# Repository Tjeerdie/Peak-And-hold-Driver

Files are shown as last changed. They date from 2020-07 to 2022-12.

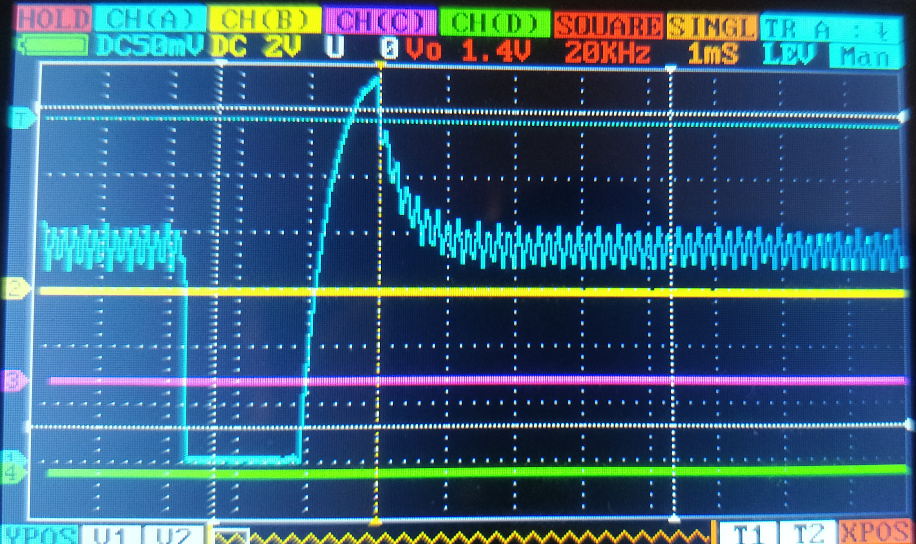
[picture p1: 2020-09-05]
Measurements/CoilCurrent_85procentDutycycle4500RPM3.5APeak2.0AHold.jpg

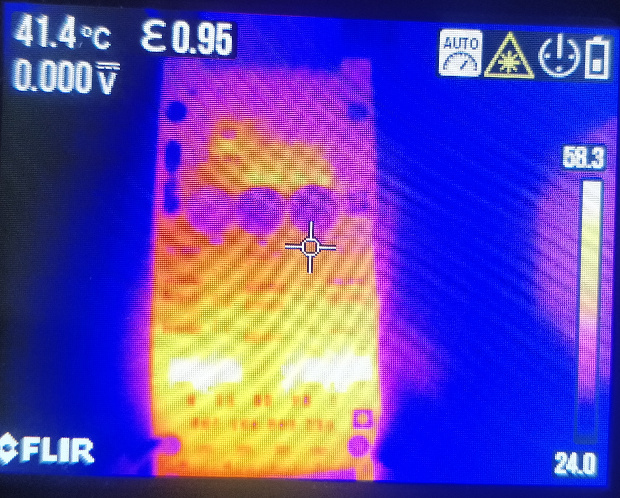
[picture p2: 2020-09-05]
Measurements/HeatMap_85procentDutycycle4500RPM3.5APeak1.0AHold.jpg

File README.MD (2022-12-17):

# Project PWM peak and hold injector driver
The peak and hold project started because I could not find an open-source PWM peak and hold injector driver for low-Z injectors. For low-z injectors normally resistors in series with the injectors are used. But resistors create a lot of heat and are not very adjustable. 

I still do encourage everyone to use resistors if possible because the results are good and resistors have less components that can fail<br/>
<br/>
This design is specific to work with LPG injectors but could be used for any other low-Z injectors like TBI type and other high flow injectors. It could even be used for any coil type actuator like relays or valves <br/>

The board is designed in Kicad. So to see the schematic or to adjust the design to your liking open the Kicad project.<br/>

Latest release is V0.3.1<br/>
__IMPORANT NOTE: Board V0.3.1 is not tested yet!! A modified V0.3 is used for bench testing the V0.3.1 schematic. I did not test the board on a car yet__<br/>
__specifications:__
- Max peak current ~5A<br/>
- Max continuous hold current ~1A (No extra cooling)<br/>
- Max continuous hold current ~2A (With extra cooling)<br/>
- Hold PWM duty cycle 5%-95%<br/>
- PWM frequency 7khz<br/>
- 4 Individual injector channels<br/>
- Peak and hold current are adjustable

## Getting Started
This section explains all we need to do to setup a fabricated PCB

### Get all the parts
1. Order the PCB. For example use https://www.pcbway.com/ or https://jlcpcb.com/ Upload the PeakHoldPWMDriver_V0.x.y.zip located in the gebers folder and order the design.<br/>
2. Get all the parts from you favorite supplier. A BOM list is included in the geber folder<br/>
3. Assemble the PCB, hand soldering is possible.<br/>

### Connect the board
The board is intended to be connected to any ECU that uses a switch to ground for each injector channel. This is the case for most types of ECU. Further down this readme there is a description how to use microcontroller pins to drive the injectors directly. <br/>

__Connector J1__
1. injector channel 1 IN<br/>
2. injector channel 2 IN<br/>
3. injector channel 3 IN<br/>
4. injector channel 4 IN<br/>
5. Power - <br/>
6. Power + (14.8V switched with ignition switch)<br/>

__Connector J2__
1. inj channel 1 +<br/>
2. inj channel 1 -<br/>
3. inj channel 2 +<br/>
4. inj channel 2 -<br/>
5. inj channel 3 +<br/>
6. inj channel 3 -<br/>
7. inj channel 4 +<br/>
8. inj channel 4 -<br/>

Power on the board. Led must be lit when powered.<br/>

### Set the PEAK current
1. Measure __TP1__ and use __RV2__ to set to value needed. 100mV = 1A<br/>
2. Make sure this PEAK current is not too close to the maximum current. If that is the case you run the risk the peak current is never reached and the HOLD current is never set. Maximum advised peak current = 10.0[V] / R-inj[Ohm]<br/>

### Set the HOLD current
1. Measure the resistance of the injector(s) per channel (R-inj)[Ohm]. <br/>
2. Find the hold current needed for the injector in the datasheet. Usually about 50% to 25% of the peak current would be enough<br/>
3. Calculate the duty cycle needed using: ((R-inj + 0.20)* HoldCurrent)/2,4<br/>
4. Measure __TP2__ and use __RV1__ to set it to voltage calculated in step 3.<br/>
5. If it is possible in your setup or on a bench, connect __injector channel 1 IN__ to the __Power -__ use a multi-meter in series with your connected injector on channel 1 to measure the current. This must be close the the set current. If this is not correct adjust __RV1__ accordingly. Be careful when doing this test! When fuel pressure is present during testing the injector under test wil spray (a lot) of fuel! Its best to test with not pressurised injectors<br/>

### Direct microcontroller input
It is possible to use the board directly with an microcontroller. (non inverted inputs) The board inputs are designed for 5V. 3.3V can work but is on the edge so any voltage drop or temperature change may make it stop working correctly. <br/>

With a sharp object scratch the bridge between __pin 1__ and __pin 2__ of __JP1__, __JP2__, __JP3__, __JP4__ on the back of the board. Use a multi-meter to double check the connection is broken. Use a soldering iron and a bit of solder to connect __pin 3__ and __pin 2__ for __JP1__ to __JP4__. The second step is to remove R8, R25, R11, R28 from the board<br/> 
       
## Simulation	
An LTspice simulation of PWM peak and hold drivers is also in the LTspice folder. It is a good learning experience to see the wave forms and the current thru the coil. This also shows the maximum voltage level expected on the mosfets. This can be significant voltage levels depdending on the clamping voltage of the main driver. <br/>

## License
This project is licensed under the GNU GENERAL PUBLIC LICENSE - see the [LICENSE.md](LICENSE.md) file for details<br/>

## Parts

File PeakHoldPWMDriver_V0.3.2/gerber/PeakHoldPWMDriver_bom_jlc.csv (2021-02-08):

Comment | Designator | Footprint | LCSC Part #
1mF | C3,C2,C1 | CP_Elec_10x12.5 | C249474
220nf | C6,C5,C14,C12,C11,C10,C9,C13,C8 | C_0603_1608Metric_Pad1.05x0.95mm_HandSolder | C21120
10uf | C7,C4 | C_1206_3216Metric_Pad1.42x1.75mm_HandSolder | C13585
LL4148 | D3 | D_MiniMELF | C9808
BLUE | D4 | LED_0603_1608Metric_Pad1.05x0.95mm_HandSolder | C375446
BAT54S | D6,D14,D13,D5 | SOT-23 | C19726
SS36 | D20,D19,D12,D11 | D_SMC | C35722
PPTC 16V2A | F2 | Fuse_1812_4532Metric_Pad1.30x3.40mm_HandSolder | C70115
TSM2309 | Q5,Q15,Q13,Q6,Q19,Q17,Q18,Q20 | SOT-23 | C15127
2N7002 | Q12,Q11,Q4,Q1,Q2,Q10,Q9,Q3 | SOT-23 | C8545
IRLL 024N | Q16,Q14,Q8,Q7 | SOT-223 | C189606
470k | R3 | R_0603_1608Metric_Pad1.05x0.95mm_HandSolder | C23178
100k | R4 | R_0603_1608Metric_Pad1.05x0.95mm_HandSolder | C25803
15k | R5 | R_0603_1608Metric_Pad1.05x0.95mm_HandSolder | C22809
470R | R6,R32,R35,R34,R16,R19,R15,R17,R7,R9,R12,R29,R31,R26 | R_0603_1608Metric_Pad1.05x0.95mm_HandSolder | C23179
10K | R8,R11,R28,R25,R44,R43,R41 | R_0603_1608Metric_Pad1.05x0.95mm_HandSolder | C25804
10k | R10 | R_0603_1608Metric_Pad1.05x0.95mm_HandSolder | C25804
0R1 | R22,R38,R21,R37 | R_2512_6332Metric_Pad1.52x3.35mm_HandSolder | C76254
1K | R24,R39,R40,R23,R13,R14,R30,R27,R42 | R_0603_1608Metric_Pad1.05x0.95mm_HandSolder | C21190
100R | R33,R36,R20,R18 | R_0603_1608Metric_Pad1.05x0.95mm_HandSolder | C22775
120k | R45 | R_0603_1608Metric | C25808
33k | R47 | R_0603_1608Metric | C4216
74HC32 | U1 | SO-14_5.3x10.2mm_P1.27mm | C5632
LM2901 | U2 | SO-14_5.3x10.2mm_P1.27mm | C163545
LTC6992 | U4 | SOT-23-6_Handsoldering | C117381
74HC74 | U5,U3 | SO-14_5.3x10.2mm_P1.27mm | C7345
LM340 | U6 | SOT-223-3_TabPin2 | C131990
74HC08 | U7,U8 | SO-14_5.3x10.2mm_P1.27mm | C5593

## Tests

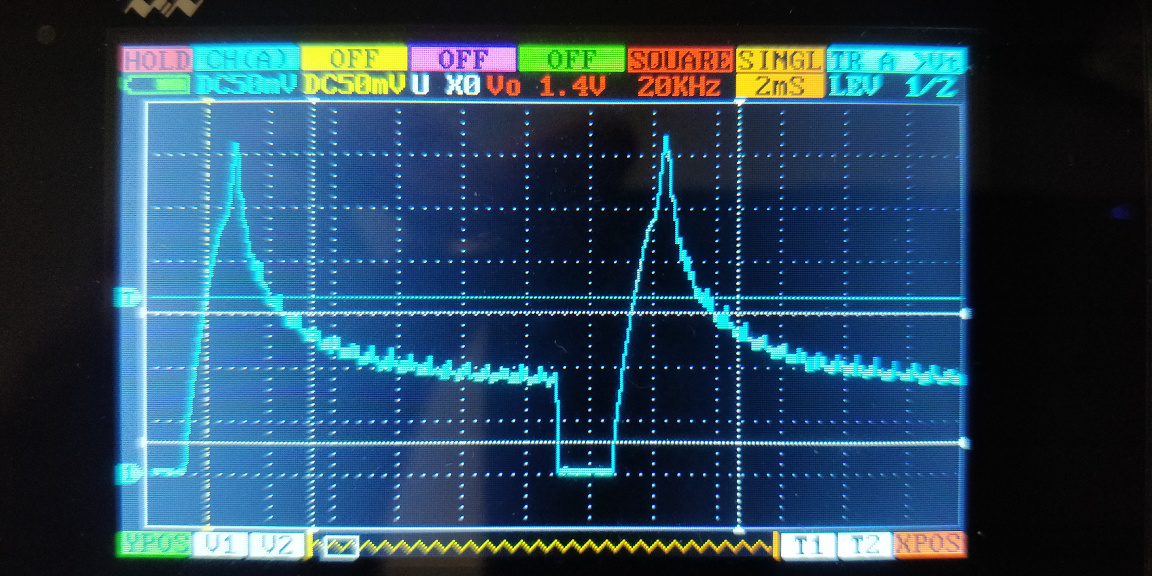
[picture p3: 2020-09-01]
Measurements/CoilCurrent_95procentDutycycle4500RPM3.5APeak0.8AHold.jpg

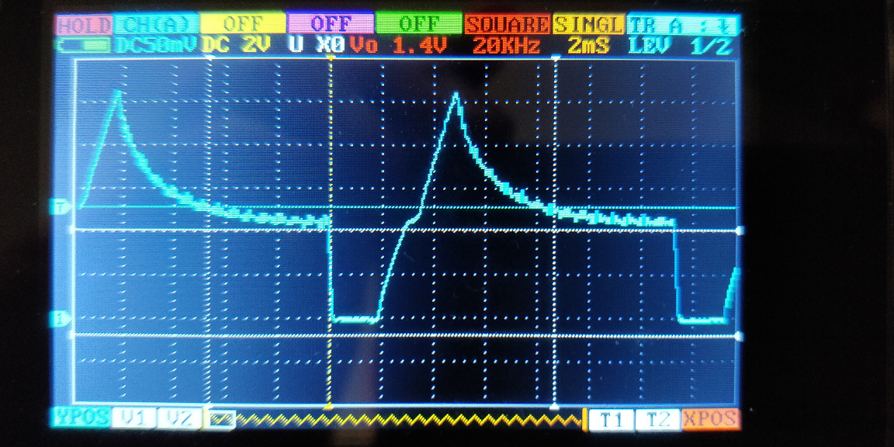
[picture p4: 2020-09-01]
Measurements/CoilCurrent_95procentDutycycle4500RPM2.5APeak1.1AHold.jpg

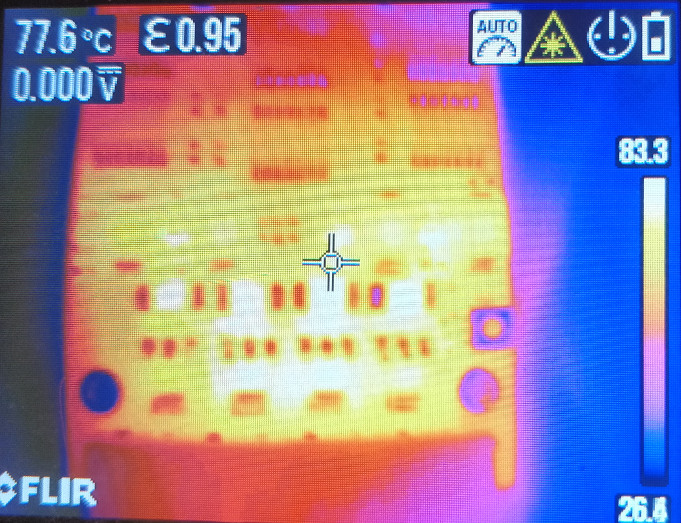
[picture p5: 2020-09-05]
Measurements/HeatMap_85procentDutycycle4500RPM3.5APeak2.0AHold.jpg

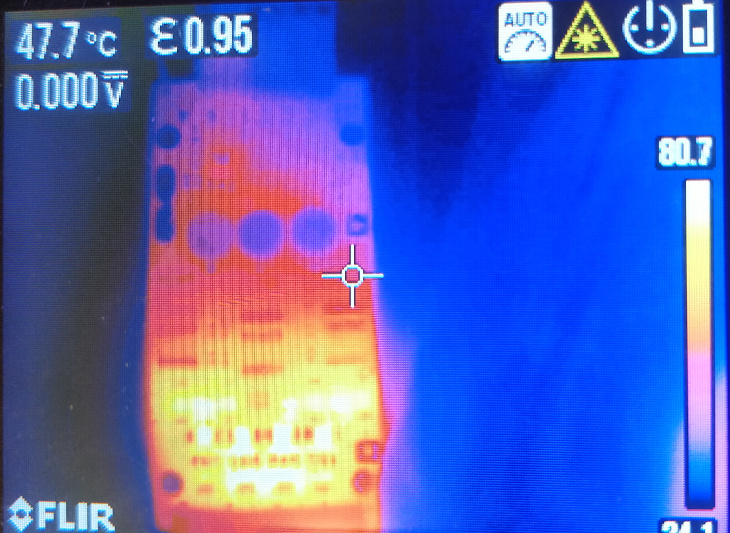
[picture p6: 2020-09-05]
Measurements/HeatMap_85procentDutycycle4500RPM3.5APeak2.0AHold_2.jpg

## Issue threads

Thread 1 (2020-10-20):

TSM2309

hugovw1976, 2020-10-20:
Hi, just curious why you use two TSM2309 in parallel.

Tjeerdie, 2020-10-20:
There is little more explanation on the speeduino forum for this board.

The reasoning is heat dissipation. Its a sot23 package. Two parallel will
give you half the Rds on and two packages to get the heat out. With 1A you
maybe get away with one.

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

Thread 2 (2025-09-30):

BOM and CPL not matching

alexsve1990, 2025-09-30:
I'm trying to upload the BOM and CPL file after I have uploaded the Gerber file. I get a mismatch with some components missing in the BOM file and sometimes I also get error messages. I also tried with different versions of Gerber file.

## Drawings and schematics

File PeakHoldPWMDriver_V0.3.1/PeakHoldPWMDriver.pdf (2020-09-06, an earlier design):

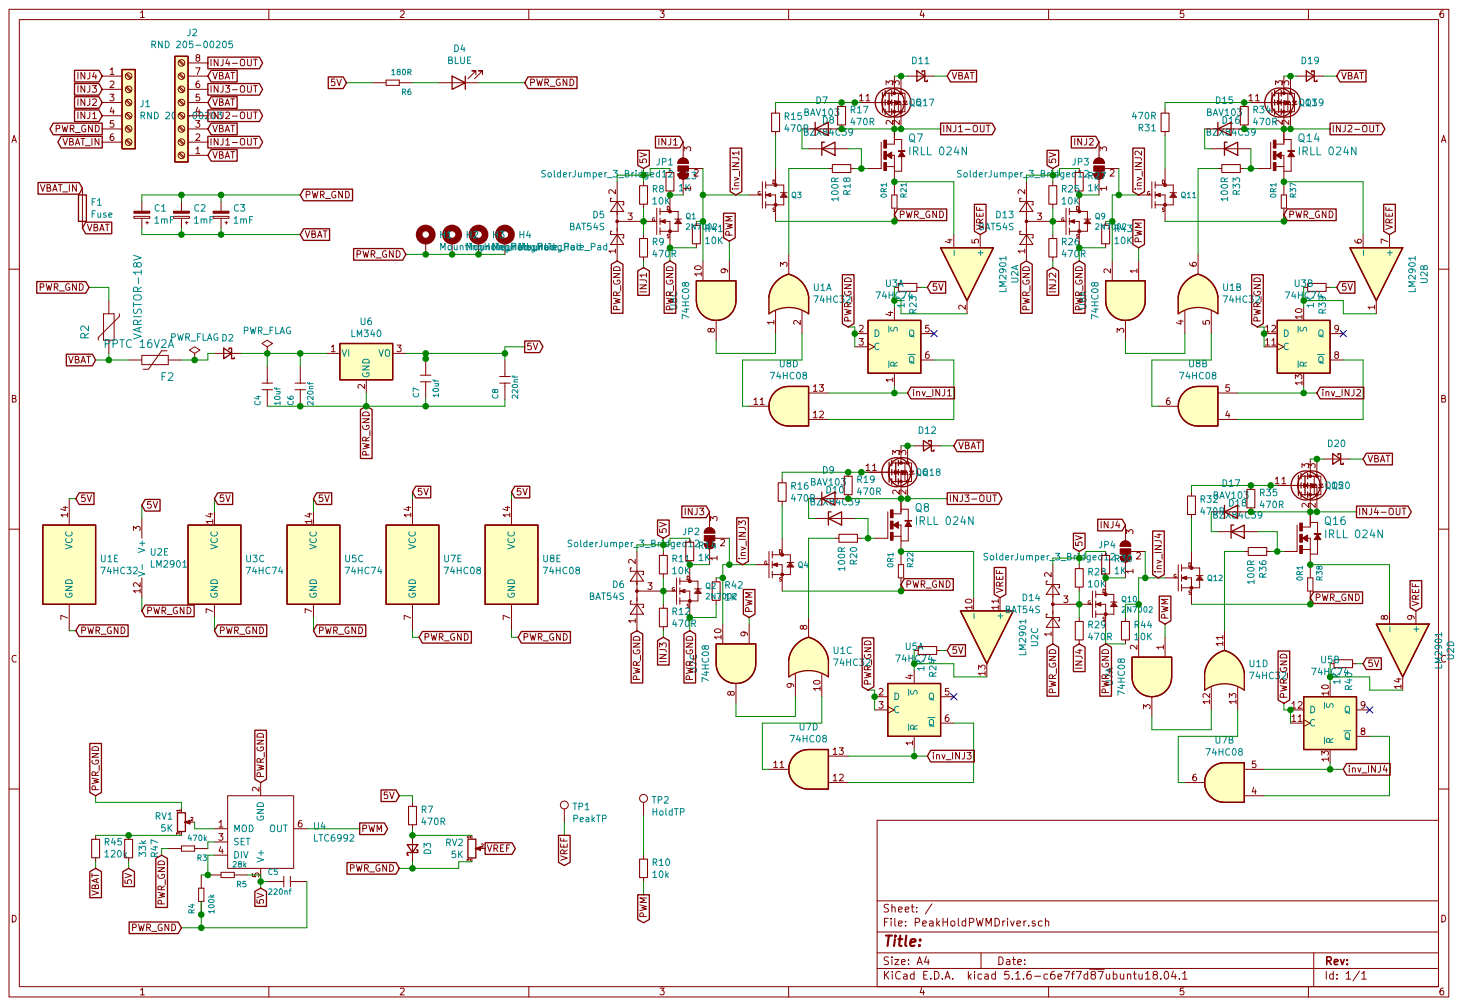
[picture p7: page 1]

Id: 1/1 Title: File: PeakHoldPWMDriver.sch Sheet: / VCC 14 GND

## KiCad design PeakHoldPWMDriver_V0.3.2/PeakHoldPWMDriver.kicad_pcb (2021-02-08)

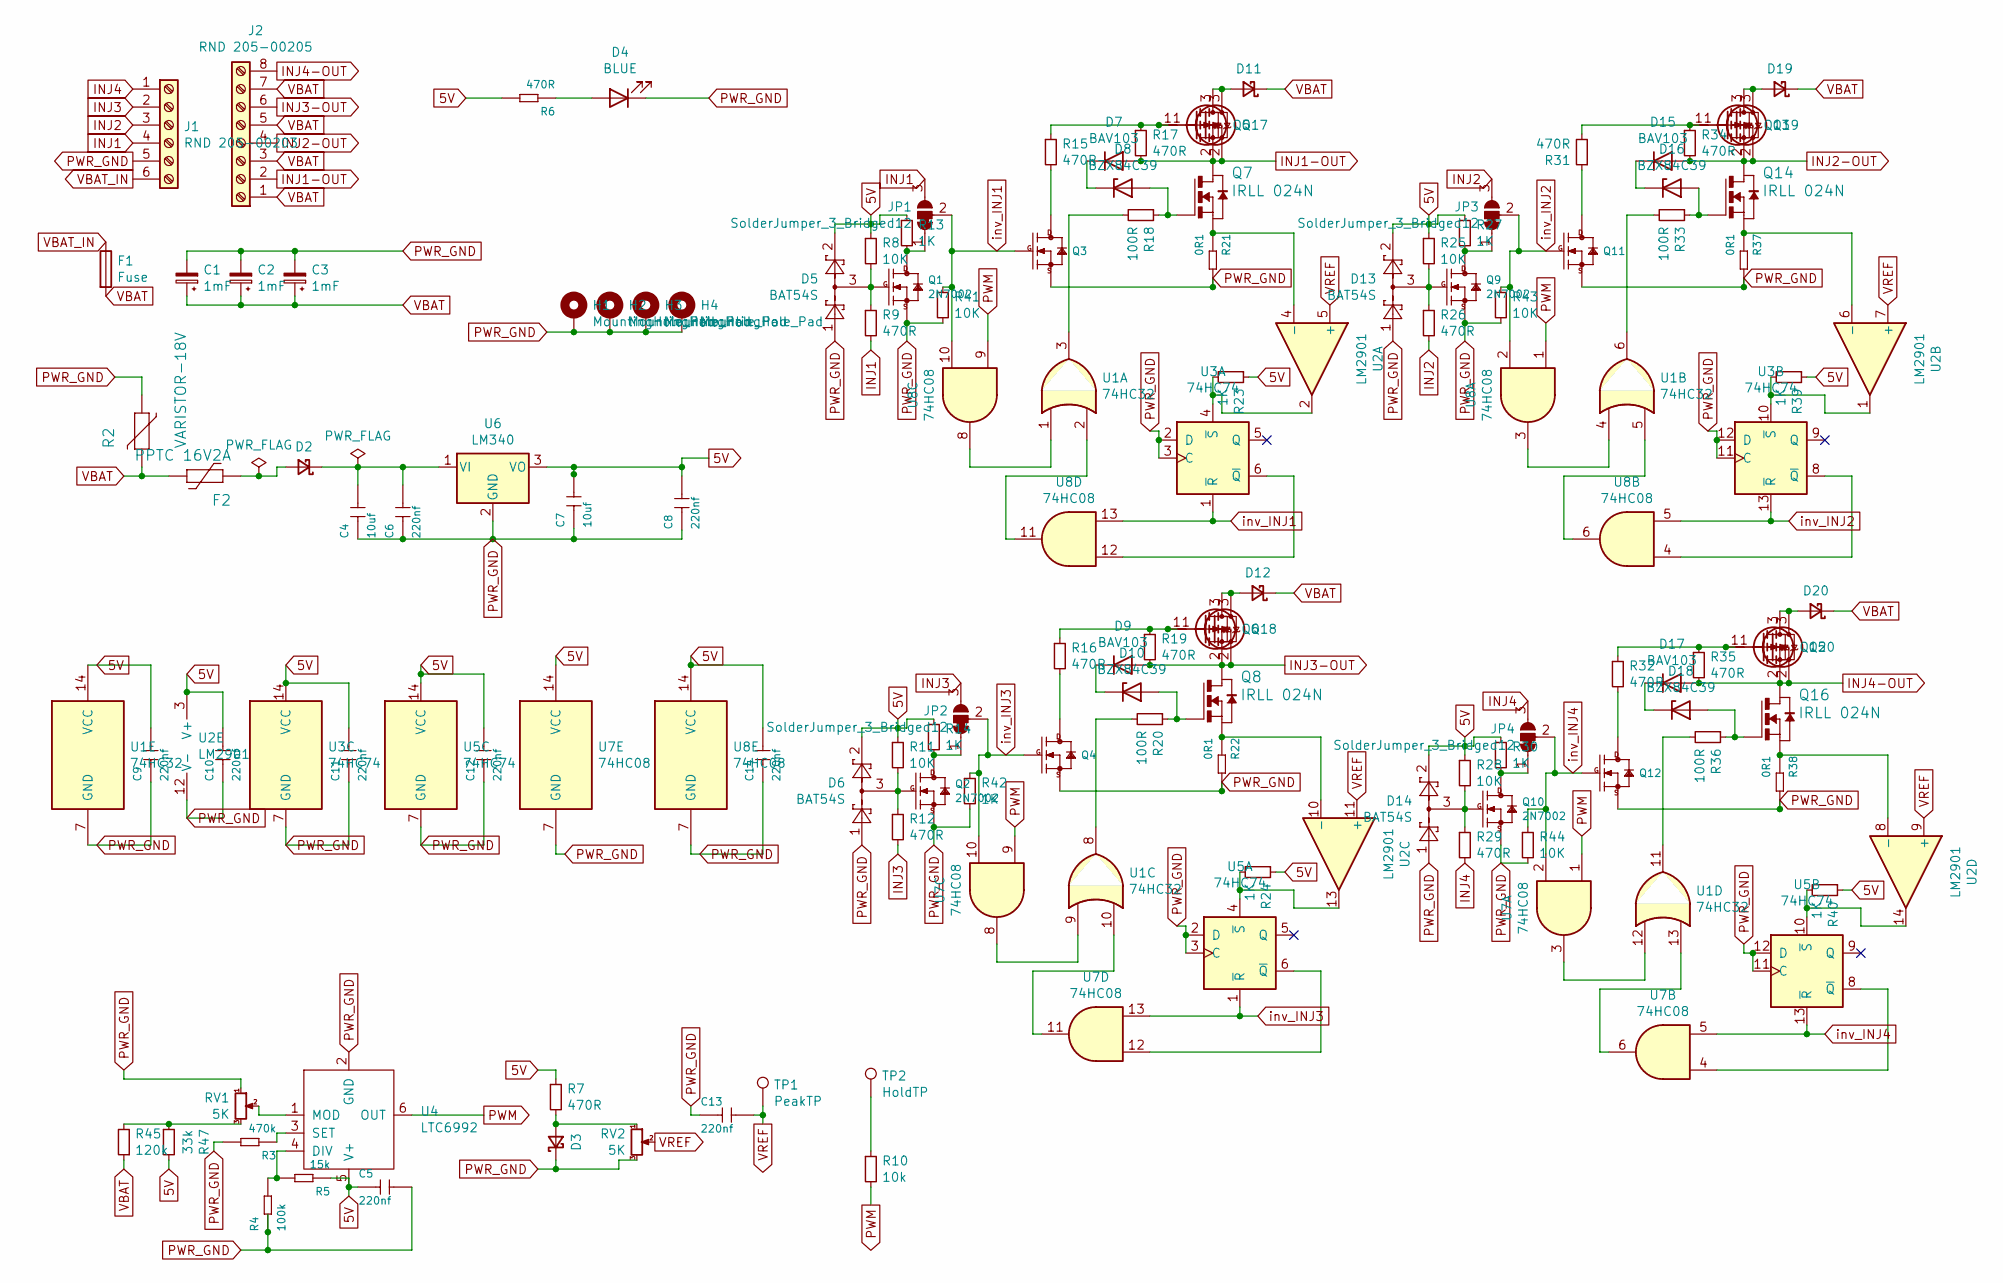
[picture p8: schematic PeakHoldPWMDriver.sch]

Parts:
C1, C2, C3: 1mF; CP_Elec_10x12.5; LCSC Part # C249474 C249474
C4, C7: 10uf; C_1206_3216Metric_Pad1.42x1.75mm_HandSolder; LCSC C13585
C5, C6, C8, C9, C10, C11, C12, C13, C14: 220nf; C_0603_1608Metric_Pad1.05x0.95mm_HandSolder; LCSC C21120
D2: 1N4007; D_SMA
D3: LL4148; D_MiniMELF; LCSC C9808
D4: BLUE; LED_0603_1608Metric_Pad1.05x0.95mm_HandSolder; LCSC C375446
D5, D6, D13, D14: BAT54S; SOT-23; LCSC C19726
D7, D9, D15, D17: BAV103; D_MiniMELF
D8, D10, D16, D18: BZX84C39; D_SOT-23_ANK
D11: SS36; D_SMC; LCSC C35722
D12, D19, D20: SS36; D_SMC
F1: Fuse; Fuse_Blade_ATO_directSolder
F2: PPTC 16V2A; Fuse_1812_4532Metric_Pad1.30x3.40mm_HandSolder; LCSC Part C70115
H1, H2, H3, H4: MountingHole_Pad; MountingHole_2.5mm_Pad
J1: RND 205-00203; PhoenixContact_MSTBA_2,5_6-G-5,08_1x06_P5.08mm_Horizontal
J2: RND 205-00205; PhoenixContact_MSTBA_2,5_8-G-5,08_1x08_P5.08mm_Horizontal
JP1, JP2, JP3, JP4: SolderJumper_3_Bridged12; SolderJumper-3_P1.3mm_Bridged12_Pad1.0x1.5mm
Q1, Q3: 2N7002; SOT-23; LCSC C8545
Q2, Q4, Q9, Q10, Q11, Q12: 2N7002; SOT-23
Q5, Q17: TSM2309; SOT-23; LCSC C15127
Q6, Q13, Q15, Q18, Q19, Q20: TSM2309; SOT-23
Q7: IRLL 024N; SOT-223; LCSC C189606
Q8, Q14, Q16: IRLL 024N; SOT-223
R2: VARISTOR-18V; RV_Disc_D12mm_W3.9mm_P7.5mm
R3: 470k; R_0603_1608Metric_Pad1.05x0.95mm_HandSolder
R4: 100k; R_0603_1608Metric_Pad1.05x0.95mm_HandSolder; LCSC C25803
R5: 15k; R_0603_1608Metric_Pad1.05x0.95mm_HandSolder; LCSC C22809
R6, R7, R9, R15, R17: 470R; R_0603_1608Metric_Pad1.05x0.95mm_HandSolder; LCSC C23179
R8, R41: 10K; R_0603_1608Metric_Pad1.05x0.95mm_HandSolder; LCSC C25804
R10: 10k; R_0603_1608Metric_Pad1.05x0.95mm_HandSolder; LCSC C25804
R11, R25, R28, R43, R44: 10K; R_0603_1608Metric_Pad1.05x0.95mm_HandSolder
R12, R16, R19, R26, R29, R31, R32, R34, R35: 470R; R_0603_1608Metric_Pad1.05x0.95mm_HandSolder
R13, R23: 1K; R_0603_1608Metric_Pad1.05x0.95mm_HandSolder; LCSC C21190
R14, R24, R27, R30, R39, R40, R42: 1K; R_0603_1608Metric_Pad1.05x0.95mm_HandSolder
R18: 100R; R_0603_1608Metric_Pad1.05x0.95mm_HandSolder; LCSC C22775
R20, R33, R36: 100R; R_0603_1608Metric_Pad1.05x0.95mm_HandSolder
R21: 0R1; R_2512_6332Metric_Pad1.52x3.35mm_HandSolder; LCSC C76254
R22, R37, R38: 0R1; R_2512_6332Metric_Pad1.52x3.35mm_HandSolder
R45: 120k; R_0603_1608Metric; LCSC C25808
R47: 33k; R_0603_1608Metric
RV1, RV2: 5K; Potentiometer_Bourns_3314R-1_Vertical_Hole
TP1: PeakTP; TestPoint_Pad_1.0x1.0mm
TP2: HoldTP; TestPoint_Pad_1.0x1.0mm
U1: 74HC32; SO-14_5.3x10.2mm_P1.27mm
U2: LM2901; SO-14_5.3x10.2mm_P1.27mm
U3: 74HC74; SO-14_5.3x10.2mm_P1.27mm; LCSC C7345
U4: LTC6992; SOT-23-6_Handsoldering; LCSC Part # C117381 C117381
U5: 74HC74; SO-14_5.3x10.2mm_P1.27mm
U6: LM340; SOT-223-3_TabPin2; LCSC Part # C131990 C131990
U7, U8: 74HC08; SO-14_5.3x10.2mm_P1.27mm

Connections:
5V: C5.1, C7.2, C8.2, C9.2, C10.2, C11.2, C12.2, C14.2, D5.2, D6.2, D13.2, D14.2, R5.1, R6.2, R7.1, R8.1, R11.1, R13.1, R14.1, R23.1, R24.1, R25.1, R27.1, R28.1, R30.1, R39.1, R40.1, R47.2, U1.14 (VCC), U2.3 (V+), U3.14 (VCC), U4.5 (V+), U5.14 (VCC), U6.3 (VO), U7.14 (VCC), U8.14 (VCC)
INJ1: J1.4, JP1.3 (B), R9.2
INJ1-OUT: D7.2 (A), J2.2, Q5.2 (S), Q7.2 (D), Q7.4 (D), Q17.2 (S), R17.2
INJ2: J1.3, JP3.3 (B), R26.2
INJ2-OUT: D15.2 (A), J2.4, Q13.2 (S), Q14.2 (D), Q14.4 (D), Q19.2 (S), R34.2
INJ3: J1.2, JP2.3 (B), R12.2
INJ3-OUT: D9.2 (A), J2.6, Q6.2 (S), Q8.2 (D), Q8.4 (D), Q18.2 (S), R19.2
INJ4: J1.1, JP4.3 (B), R29.2
INJ4-OUT: D17.2 (A), J2.8, Q15.2 (S), Q16.2 (D), Q16.4 (D), Q20.2 (S), R35.2
unnamed: C4.2, C6.2, D2.1 (K), U6.1 (VI)
unnamed: D2.2 (A), F2.2
unnamed: D3.2 (A), R7.2, RV2.1
unnamed: D4.2 (A), R6.1
unnamed: D5.3, Q1.1 (G), R8.2, R9.1
unnamed: D6.3, Q2.1 (G), R11.2, R12.1
unnamed: D7.1 (K), D8.1 (K)
unnamed: D8.2 (A), Q7.1 (G), R18.1
unnamed: D9.1 (K), D10.1 (K)
unnamed: D10.2 (A), Q8.1 (G), R20.1
unnamed: D11.2 (A), Q5.3 (D), Q17.3 (D)
unnamed: D12.2 (A), Q6.3 (D), Q18.3 (D)
unnamed: D13.3, Q9.1 (G), R25.2, R26.1
unnamed: D14.3, Q10.1 (G), R28.2, R29.1
unnamed: D15.1 (K), D16.1 (K)
unnamed: D16.2 (A), Q14.1 (G), R33.1
unnamed: D17.1 (K), D18.1 (K)
unnamed: D18.2 (A), Q16.1 (G), R36.1
unnamed: D19.2 (A), Q13.3 (D), Q19.3 (D)
unnamed: D20.2 (A), Q15.3 (D), Q20.3 (D)
unnamed: JP1.1 (A), Q1.3 (D), R13.2
unnamed: JP2.1 (A), Q2.3 (D), R14.2
unnamed: JP3.1 (A), Q9.3 (D), R27.2
unnamed: JP4.1 (A), Q10.3 (D), R30.2
unnamed: Q3.3 (D), R15.2
unnamed: Q4.3 (D), R16.2
unnamed: Q7.3 (S), R21.1, U2.4 (-)
unnamed: Q8.3 (S), R22.1, U2.10 (-)
unnamed: Q11.3 (D), R31.1
unnamed: Q12.3 (D), R32.2
unnamed: Q13.1 (G), Q19.1 (G), R31.2, R34.1
unnamed: Q14.3 (S), R37.1, U2.6 (-)
unnamed: Q15.1 (G), Q20.1 (G), R32.1, R35.1
unnamed: Q16.3 (S), R38.1, U2.8 (-)
unnamed: Q5.1 (G), Q17.1 (G), R15.1, R17.1
unnamed: Q6.1 (G), Q18.1 (G), R16.1, R19.1
unnamed: R3.1, U4.3 (SET)
unnamed: R4.2, R5.2, U4.4 (DIV)
unnamed: R10.1, TP2.1
unnamed: R18.2, U1.3
unnamed: R20.2, U1.8
unnamed: R23.2, U2.2, U3.4 (~S)
unnamed: R24.2, U2.13, U5.4 (~S)
unnamed: R33.2, U1.6
unnamed: R36.2, U1.11
unnamed: R39.2, U2.1, U3.10 (~S)
unnamed: R40.2, U2.14, U5.10 (~S)
unnamed: R45.2, R47.1, RV1.3
unnamed: RV1.2, U4.1 (MOD)
unnamed: U1.1, U8.8
unnamed: U1.2, U8.11
unnamed: U1.4, U8.3
unnamed: U1.5, U8.6
unnamed: U1.9, U7.8
unnamed: U1.10, U7.11
unnamed: U1.12, U7.3
unnamed: U1.13, U7.6
unnamed: U3.6 (~Q), U8.12
unnamed: U3.8 (~Q), U8.4
unnamed: U5.6 (~Q), U7.12
unnamed: U5.8 (~Q), U7.4
PWM: R10.2, U4.6 (OUT), U7.1, U7.9, U8.1, U8.9
PWR_GND: C1.2, C2.2, C3.2, C4.1, C5.2, C6.1, C7.1, C8.1, C9.1, C10.1, C11.1, C12.1, C13.1, C14.1, D3.1 (K), D4.1 (K), D5.1, D6.1, D13.1, D14.1, H1.1, H2.1, H3.1, H4.1, J1.5, Q1.2 (S), Q2.2 (S), Q3.2 (S), Q4.2 (S), Q9.2 (S), Q10.2 (S), Q11.2 (S), Q12.2 (S), R2.1, R3.2, R4.1, R21.2, R22.2, R37.2, R38.2, R41.2, R42.2, R43.2, R44.2, RV1.1, RV2.3, U1.7 (GND), U2.12 (V-), U3.2 (D), U3.3 (C), U3.7 (GND), U3.11 (C), U3.12 (D), U4.2 (GND), U5.2 (D), U5.3 (C), U5.7 (GND), U5.11 (C), U5.12 (D), U6.2 (GND), U7.7 (GND), U8.7 (GND)
VBAT: C1.1, C2.1, C3.1, D11.1 (K), D12.1 (K), D19.1 (K), D20.1 (K), F1.2, F2.1, J2.1, J2.3, J2.5, J2.7, R2.2, R45.1
VBAT_IN: F1.1, J1.6
VREF: C13.2, RV2.2, TP1.1, U2.5 (+), U2.7 (+), U2.9 (+), U2.11 (+)
inv_INJ1: JP1.2 (C), Q3.1 (G), R41.1, U3.1 (~R), U8.10, U8.13
inv_INJ2: JP3.2 (C), Q11.1 (G), R43.1, U3.13 (~R), U8.2, U8.5
inv_INJ3: JP2.2 (C), Q4.1 (G), R42.1, U5.1 (~R), U7.10, U7.13
inv_INJ4: JP4.2 (C), Q12.1 (G), R44.1, U5.13 (~R), U7.2, U7.5

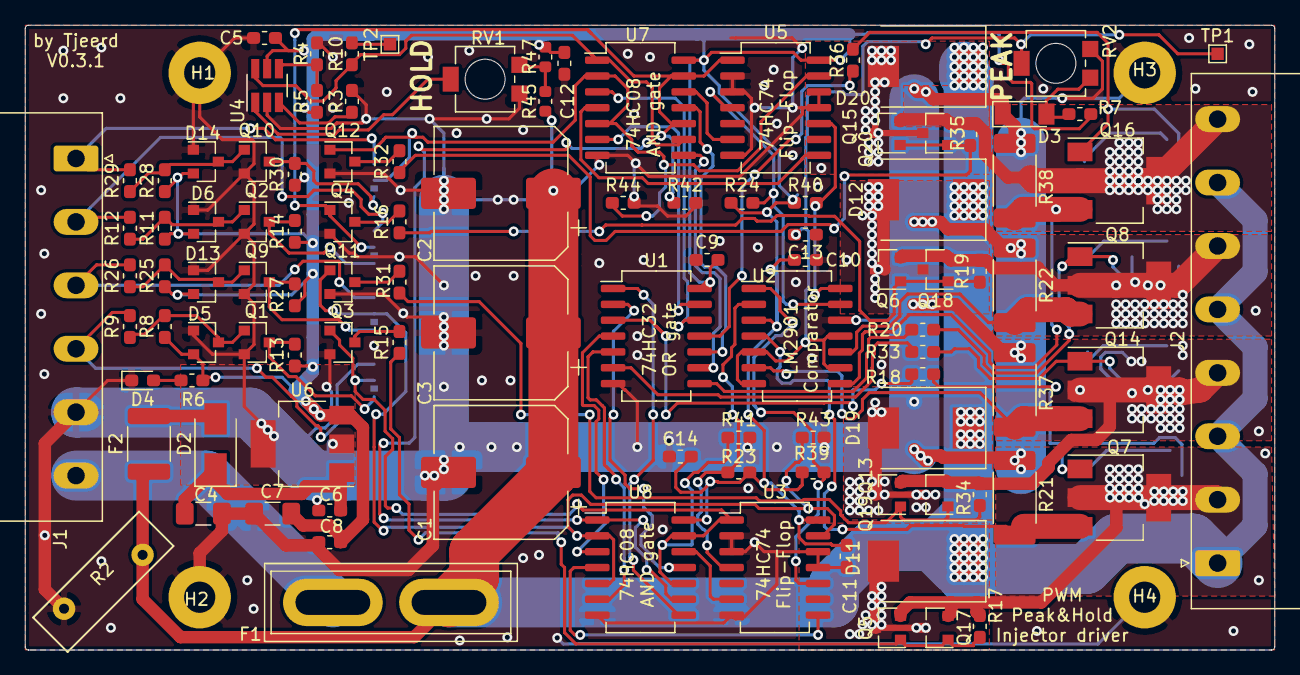
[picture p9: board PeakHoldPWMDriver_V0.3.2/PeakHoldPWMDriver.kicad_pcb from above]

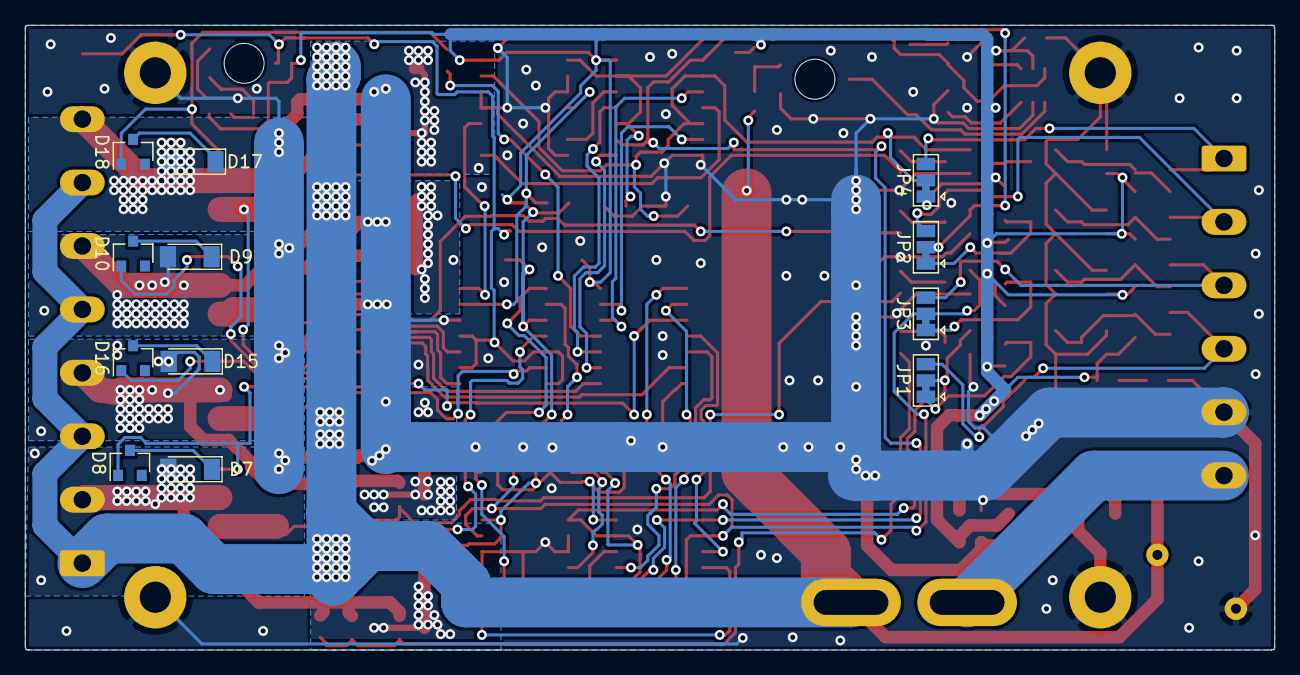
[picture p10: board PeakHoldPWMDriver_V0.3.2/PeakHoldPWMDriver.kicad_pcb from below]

Board: 2 copper layers, 100.1 x 50.0 mm, 122 parts (12 on the bottom side), 79 nets.

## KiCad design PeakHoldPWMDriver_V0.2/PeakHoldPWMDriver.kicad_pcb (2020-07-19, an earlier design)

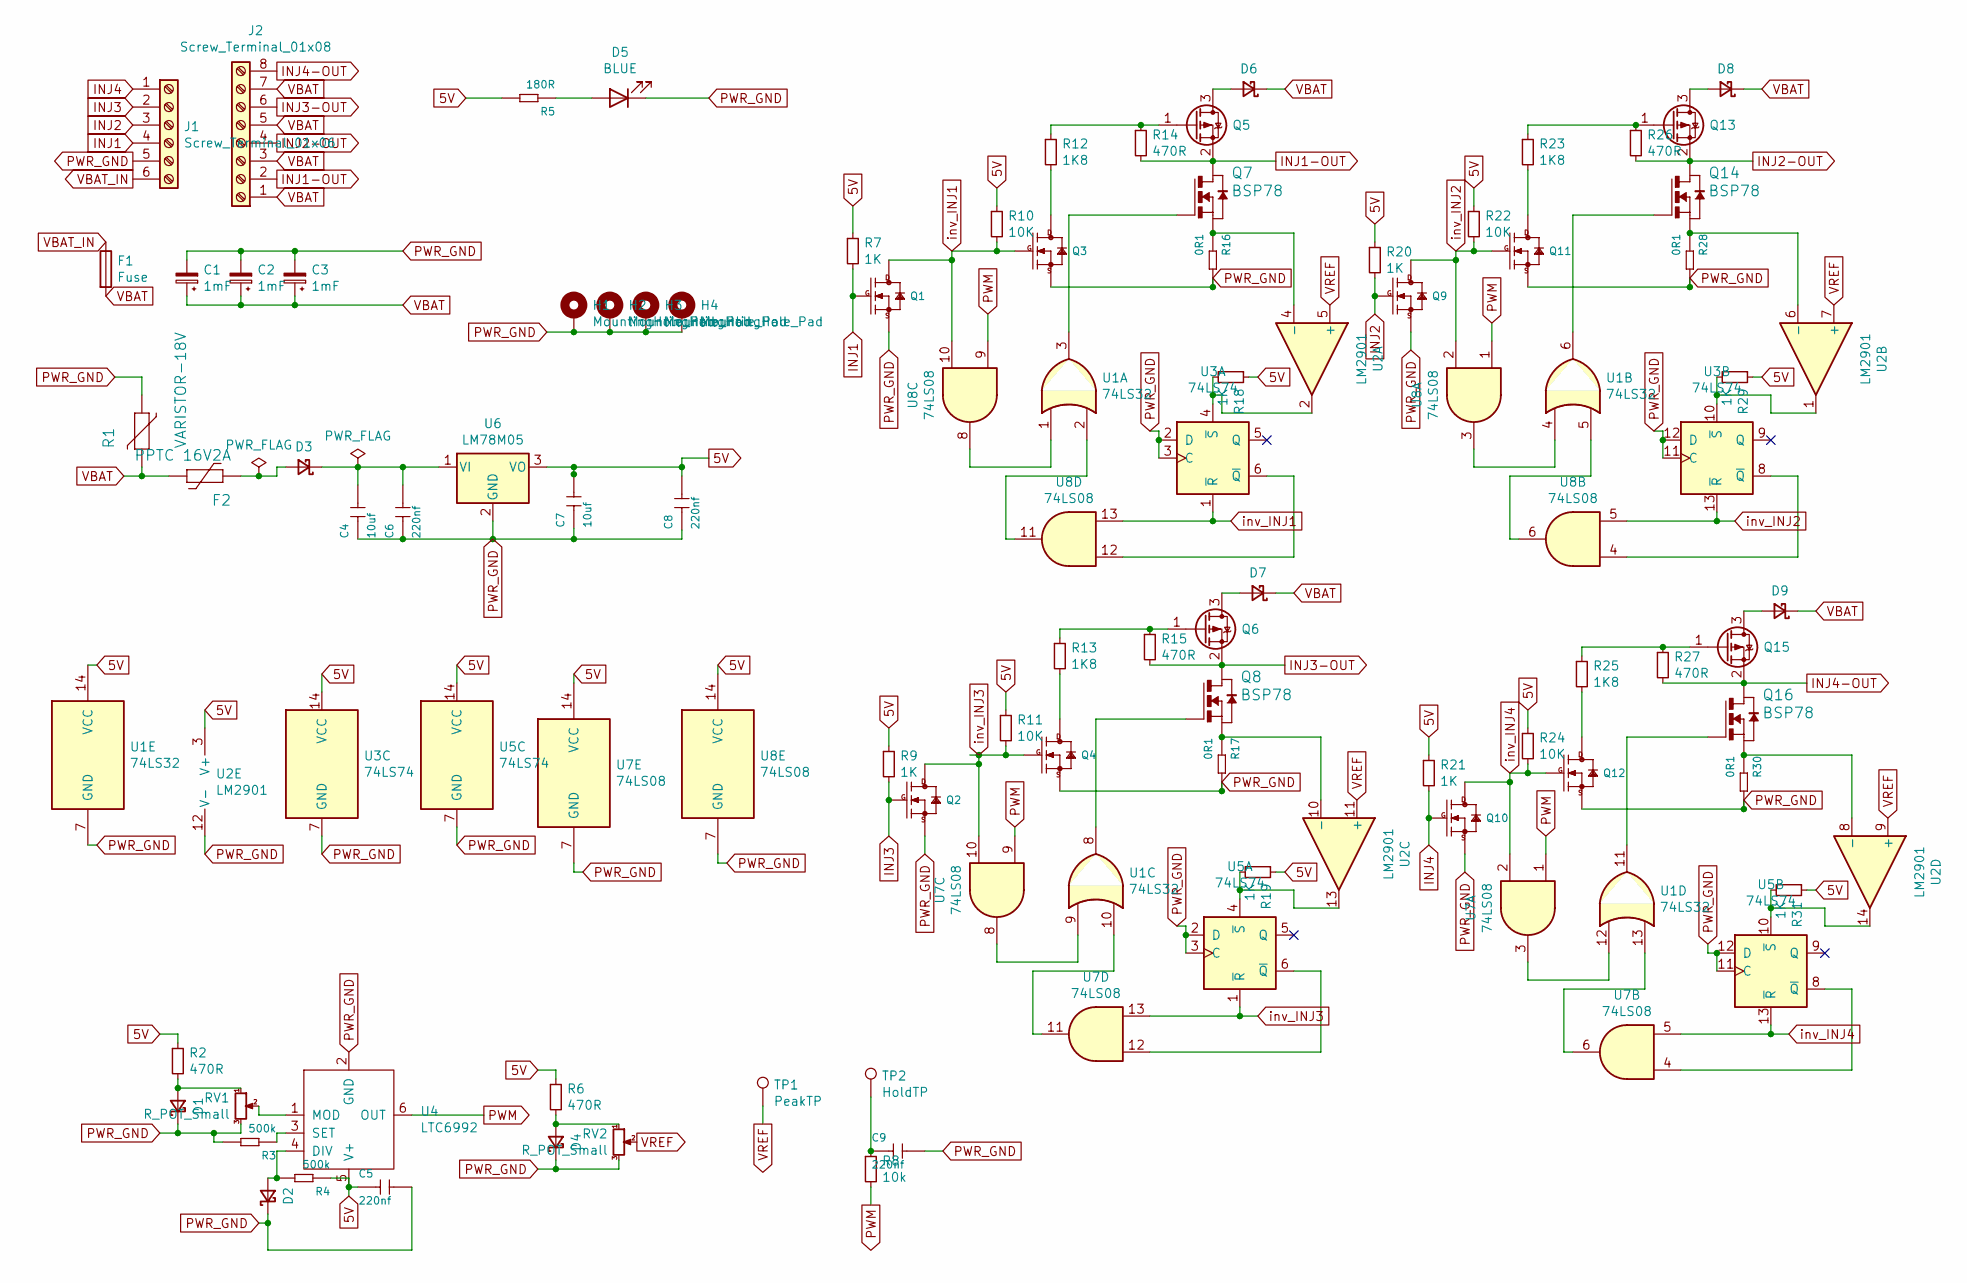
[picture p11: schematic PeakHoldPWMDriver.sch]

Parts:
C1, C2, C3: 1mF; CP_Elec_10x12.5
C4, C7: 10uf; C_1206_3216Metric_Pad1.42x1.75mm_HandSolder
C5, C6, C8, C9: 220nf; C_0603_1608Metric_Pad1.05x0.95mm_HandSolder
D1, D2, D4: BAV103; D_MiniMELF
D3: 1N4007; D_SMA
D5: BLUE; LED_0603_1608Metric_Pad1.05x0.95mm_HandSolder
D6, D7, D8, D9: SS36; D_SMA
F1: Fuse; Fuse_Blade_ATO_directSolder
F2: PPTC 16V2A; Fuse_1812_4532Metric_Pad1.30x3.40mm_HandSolder
H1, H2, H3, H4: MountingHole_Pad; MountingHole_2.5mm_Pad
J1: Screw_Terminal_01x06; PhoenixContact_MSTBA_2,5_6-G-5,08_1x06_P5.08mm_Horizontal
J2: Screw_Terminal_01x08; PhoenixContact_MSTBA_2,5_8-G-5,08_1x08_P5.08mm_Horizontal
Q1, Q2, Q9, Q10: AO3400; SOT-23_Handsoldering
Q3, Q4, Q11, Q12: 2N7002; SOT-23_Handsoldering
Q5, Q6, Q13, Q15: TSM2309; SOT-23_Handsoldering
Q7, Q8, Q14, Q16: BSP78; SOT-223
R1: VARISTOR-18V; RV_Disc_D12mm_W3.9mm_P7.5mm
R2, R6, R14, R15, R26, R27: 470R; R_0603_1608Metric_Pad1.05x0.95mm_HandSolder
R3, R4: 500k; R_0603_1608Metric_Pad1.05x0.95mm_HandSolder
R5: 180R; R_0603_1608Metric_Pad1.05x0.95mm_HandSolder
R7, R9, R18, R19, R20, R21, R29, R31: 1K; R_0603_1608Metric_Pad1.05x0.95mm_HandSolder
R8: 10k; R_0603_1608Metric_Pad1.05x0.95mm_HandSolder
R10, R11, R22, R24: 10K; R_0603_1608Metric_Pad1.05x0.95mm_HandSolder
R12, R13, R23, R25: 1K8; R_0603_1608Metric_Pad1.05x0.95mm_HandSolder
R16, R17, R28, R30: 0R1; R_2512_6332Metric_Pad1.52x3.35mm_HandSolder
RV1, RV2: R_POT_Small; Potentiometer_Bourns_3314R-1_Vertical_Hole
TP1: PeakTP; TestPoint_Pad_1.0x1.0mm
TP2: HoldTP; TestPoint_Pad_1.0x1.0mm
U1: 74LS32; SO-14_5.3x10.2mm_P1.27mm
U2: LM2901; SO-14_5.3x10.2mm_P1.27mm
U3, U5: 74LS74; SO-14_5.3x10.2mm_P1.27mm
U4: LTC6992; SOT-23-6_Handsoldering
U6: LM78M05; SOT-223-3_TabPin2
U7, U8: 74LS08; SO-14_5.3x10.2mm_P1.27mm

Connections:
5V: C5.1, C7.2, C8.2, R2.1, R4.1, R5.2, R6.1, R7.1, R9.1, R10.1, R11.1, R18.1, R19.1, R20.1, R21.1, R22.1, R24.1, R29.1, R31.1, U1.14 (VCC), U2.3 (V+), U3.14 (VCC), U4.5 (V+), U5.14 (VCC), U6.3 (VO), U7.14 (VCC), U8.14 (VCC)
INJ1: J1.4, Q1.1 (G), R7.2
INJ1-OUT: J2.2, Q5.2 (S), Q7.2 (D), Q7.4 (D), R14.2
INJ2: J1.3, Q9.1 (G), R20.2
INJ2-OUT: J2.4, Q13.2 (S), Q14.2 (D), Q14.4 (D), R26.2
INJ3: J1.2, Q2.1 (G), R9.2
INJ3-OUT: J2.6, Q6.2 (S), Q8.2 (D), Q8.4 (D), R15.2
INJ4: J1.1, Q10.1 (G), R21.2
INJ4-OUT: J2.8, Q15.2 (S), Q16.2 (D), Q16.4 (D), R27.2
unnamed: C4.2, C6.2, D3.1 (K), U6.1 (VI)
unnamed: C9.1, R8.1, TP2.1
unnamed: D1.2 (A), R2.2, RV1.1
unnamed: D2.2 (A), R4.2, U4.4 (DIV)
unnamed: D3.2 (A), F2.2
unnamed: D4.2 (A), R6.2, RV2.1
unnamed: D5.2 (A), R5.1
unnamed: D6.2 (A), Q5.3 (D)
unnamed: D7.2 (A), Q6.3 (D)
unnamed: D8.2 (A), Q13.3 (D)
unnamed: D9.2 (A), Q15.3 (D)
unnamed: Q3.3 (D), R12.2
unnamed: Q4.3 (D), R13.2
unnamed: Q5.1 (G), R12.1, R14.1
unnamed: Q6.1 (G), R13.1, R15.1
unnamed: Q7.1 (G), U1.3
unnamed: Q7.3 (S), R16.1, U2.4 (-)
unnamed: Q8.1 (G), U1.8
unnamed: Q8.3 (S), R17.1, U2.10 (-)
unnamed: Q11.3 (D), R23.2
unnamed: Q12.3 (D), R25.2
unnamed: Q13.1 (G), R23.1, R26.1
unnamed: Q14.1 (G), U1.6
unnamed: Q14.3 (S), R28.1, U2.6 (-)
unnamed: Q15.1 (G), R25.1, R27.1
unnamed: Q16.1 (G), U1.11
unnamed: Q16.3 (S), R30.1, U2.8 (-)
unnamed: R3.1, U4.3 (SET)
unnamed: R18.2, U2.2, U3.4 (~S)
unnamed: R19.2, U2.13, U5.4 (~S)
unnamed: R29.2, U2.1, U3.10 (~S)
unnamed: R31.2, U2.14, U5.10 (~S)
unnamed: RV1.2, U4.1 (MOD)
unnamed: U1.1, U8.8
unnamed: U1.2, U8.11
unnamed: U1.4, U8.3
unnamed: U1.5, U8.6
unnamed: U1.9, U7.8
unnamed: U1.10, U7.11
unnamed: U1.12, U7.3
unnamed: U1.13, U7.6
unnamed: U3.6 (~Q), U8.12
unnamed: U3.8 (~Q), U8.4
unnamed: U5.6 (~Q), U7.12
unnamed: U5.8 (~Q), U7.4
PWM: R8.2, U4.6 (OUT), U7.1, U7.9, U8.1, U8.9
PWR_GND: C1.2, C2.2, C3.2, C4.1, C5.2, C6.1, C7.1, C8.1, C9.2, D1.1 (K), D2.1 (K), D4.1 (K), D5.1 (K), H1.1, H2.1, H3.1, H4.1, J1.5, Q1.2 (S), Q2.2 (S), Q3.2 (S), Q4.2 (S), Q9.2 (S), Q10.2 (S), Q11.2 (S), Q12.2 (S), R1.1, R3.2, R16.2, R17.2, R28.2, R30.2, RV1.3, RV2.3, U1.7 (GND), U2.12 (V-), U3.2 (D), U3.3 (C), U3.7 (GND), U3.11 (C), U3.12 (D), U4.2 (GND), U5.2 (D), U5.3 (C), U5.7 (GND), U5.11 (C), U5.12 (D), U6.2 (GND), U7.7 (GND), U8.7 (GND)
VBAT: C1.1, C2.1, C3.1, D6.1 (K), D7.1 (K), D8.1 (K), D9.1 (K), F1.2, F2.1, J2.1, J2.3, J2.5, J2.7, R1.2
VBAT_IN: F1.1, J1.6
VREF: RV2.2, TP1.1, U2.5 (+), U2.7 (+), U2.9 (+), U2.11 (+)
inv_INJ1: Q1.3 (D), Q3.1 (G), R10.2, U3.1 (~R), U8.10, U8.13
inv_INJ2: Q9.3 (D), Q11.1 (G), R22.2, U3.13 (~R), U8.2, U8.5
inv_INJ3: Q2.3 (D), Q4.1 (G), R11.2, U5.1 (~R), U7.10, U7.13
inv_INJ4: Q10.3 (D), Q12.1 (G), R24.2, U5.13 (~R), U7.2, U7.5

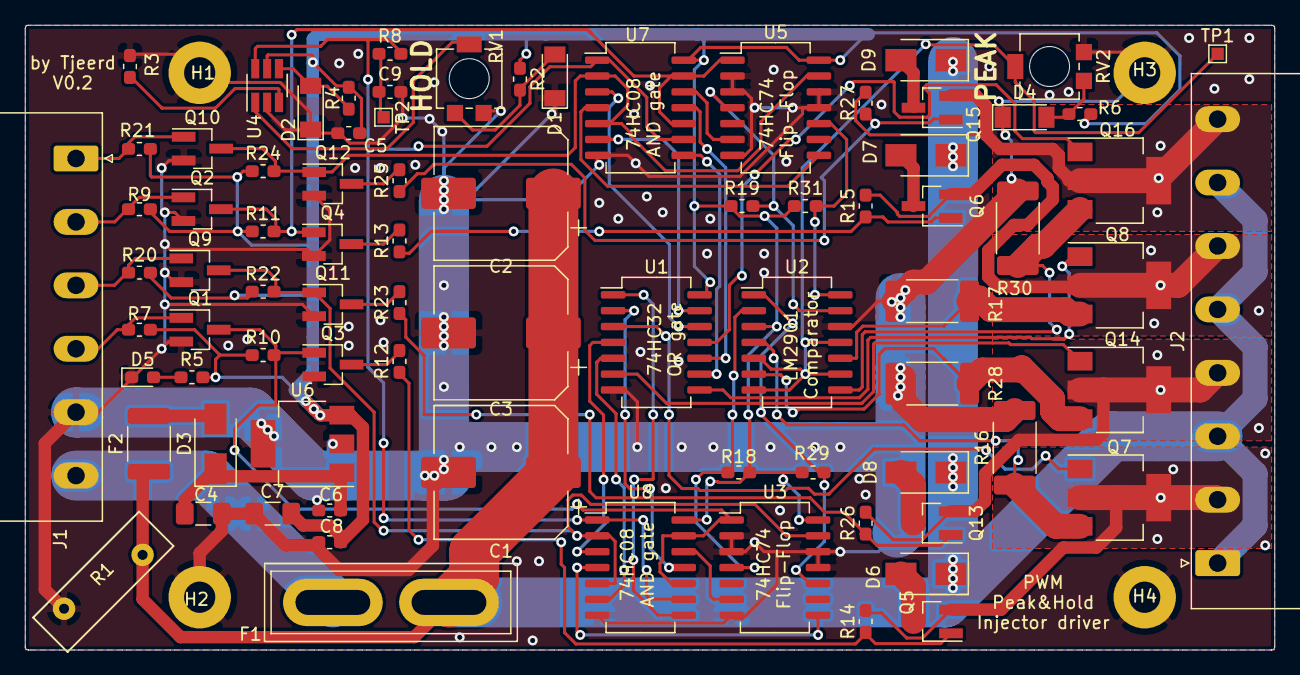
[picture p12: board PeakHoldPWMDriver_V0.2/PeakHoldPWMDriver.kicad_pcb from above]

Board: 2 copper layers, 100.1 x 50.0 mm, 85 parts (0 on the bottom side), 63 nets.

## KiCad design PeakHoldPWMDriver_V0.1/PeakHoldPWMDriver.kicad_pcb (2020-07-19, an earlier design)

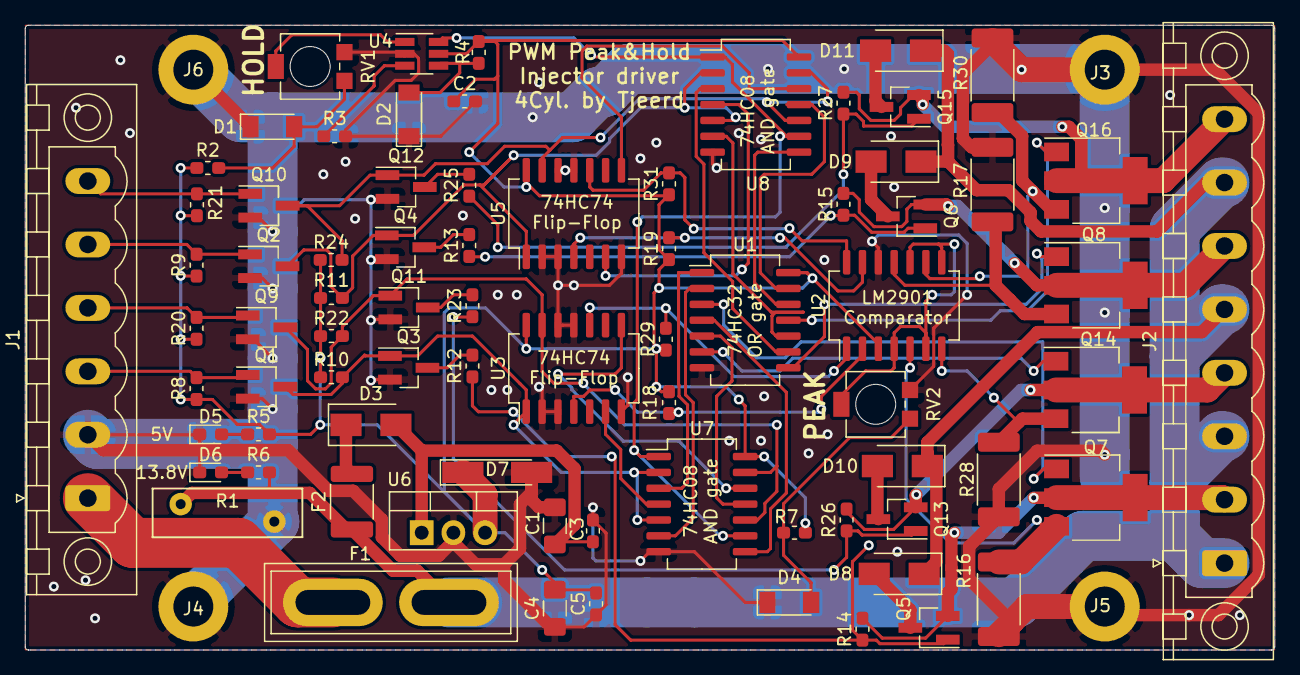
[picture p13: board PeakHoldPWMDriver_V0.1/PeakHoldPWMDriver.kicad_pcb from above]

Board: 2 copper layers, 100.1 x 50.0 mm, 81 parts (0 on the bottom side), 63 nets.

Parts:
C1, C4: 10uf; C_1206_3216Metric_Pad1.42x1.75mm_HandSolder
C2, C3, C5: 220nf; C_0603_1608Metric_Pad1.05x0.95mm_HandSolder
D1, D4: LL4148; D_MiniMELF
D2: SS310; D_MiniMELF
D3: 40V-1A; D_SMA
D5, D6: BLUE; LED_0603_1608Metric_Pad1.05x0.95mm_HandSolder
D7: D_Zener_Small; D_MiniMELF_Handsoldering
D8, D9, D10, D11: SS310; D_SMA
F1: Fuse; Fuse_Blade_ATO_directSolder
F2: PPTC 16V2A; Fuse_1812_4532Metric_Pad1.30x3.40mm_HandSolder
J1: Screw_Terminal_01x06; PhoenixContact_MSTBV_2,5_6-GF-5,08_1x06_P5.08mm_Vertical_Th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
J2: Screw_Terminal_01x08; PhoenixContact_MSTBV_2,5_8-GF-5,08_1x08_P5.08mm_Vertical_Th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
J3, J4, J5, J6: Mounting 3mm; MountingHole_3.2mm_M3_DIN965_Pad
Q1, Q2, Q9, Q10: AO3400; SOT-23_Handsoldering
Q3, Q4, Q11, Q12: AO3422; SOT-23_Handsoldering
Q5, Q6, Q13, Q15: AO3401A; SOT-23_Handsoldering
Q7, Q8, Q14, Q16: BSP78; SOT-223
R1: VARISTOR-18V; RV_Disc_D12mm_W3.9mm_P7.5mm
R2, R7, R14, R15, R26, R27: 470; R_0603_1608Metric_Pad1.05x0.95mm_HandSolder
R3, R4: 500k; R_0603_1608Metric_Pad1.05x0.95mm_HandSolder
R5: 180; R_0603_1608Metric_Pad1.05x0.95mm_HandSolder
R6: 560; R_0603_1608Metric_Pad1.05x0.95mm_HandSolder
R8, R9, R18, R19, R20, R21, R29, R31: 1K; R_0603_1608Metric_Pad1.05x0.95mm_HandSolder
R10, R11, R22, R24: 10K; R_0603_1608Metric_Pad1.05x0.95mm_HandSolder
R12, R13, R23, R25: 1K8; R_0603_1608Metric_Pad1.05x0.95mm_HandSolder
R16, R17, R28, R30: 0R1; R_2512_6332Metric_Pad1.52x3.35mm_HandSolder
RV1, RV2: R_POT_Small; Potentiometer_Bourns_3314R-1_Vertical_Hole
U1: 74LS32; SO-14_5.3x10.2mm_P1.27mm
U2: LM2901; SO-14_5.3x10.2mm_P1.27mm
U3, U5: 74LS74; SO-14_5.3x10.2mm_P1.27mm
U4: LTC6992; SOT-23-6_Handsoldering
U6: LM78M05_TO220; TO-220-3_Vertical
U7, U8: 74LS08; SO-14_5.3x10.2mm_P1.27mm

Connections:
5V: C2.1, C4.2, C5.2, D7.1, R2.1, R4.1, R5.2, R7.1, R8.1, R9.1, R10.1, R11.1, R18.1, R19.1, R20.1, R21.1, R22.1, R24.1, R29.1, R31.1, U1.14, U2.3, U3.14, U4.5, U5.14, U6.3, U7.14, U8.14
INJ1: J1.3, Q1.1, R8.2
INJ1-OUT: J2.2, Q5.2, Q7.2, Q7.4, R14.2
INJ2: J1.4, Q9.1, R20.2
INJ2-OUT: J2.4, Q13.2, Q14.2, Q14.4, R26.2
INJ3: J1.5, Q2.1, R9.2
INJ3-OUT: J2.6, Q6.2, Q8.2, Q8.4, R15.2
INJ4: J1.6, Q10.1, R21.2
INJ4-OUT: J2.8, Q15.2, Q16.2, Q16.4, R27.2
unnamed: C1.2, C3.2, D3.2, U6.1
unnamed: D1.2, R2.2, RV1.1
unnamed: D2.2, R4.2, U4.4
unnamed: D3.1, F2.2
unnamed: D4.2, R7.2, RV2.1
unnamed: D5.2, R5.1
unnamed: D6.2, R6.1
unnamed: D8.2, Q5.3
unnamed: D9.2, Q6.3
unnamed: D10.2, Q13.3
unnamed: D11.2, Q15.3
unnamed: Q3.3, R12.2
unnamed: Q4.3, R13.2
unnamed: Q5.1, R12.1, R14.1
unnamed: Q6.1, R13.1, R15.1
unnamed: Q7.1, U1.3
unnamed: Q7.3, R16.1, U2.5
unnamed: Q8.1, U1.8
unnamed: Q8.3, R17.1, U2.11
unnamed: Q11.3, R23.2
unnamed: Q12.3, R25.2
unnamed: Q13.1, R23.1, R26.1
unnamed: Q14.1, U1.6
unnamed: Q14.3, R28.1, U2.7
unnamed: Q15.1, R25.1, R27.1
unnamed: Q16.1, U1.11
unnamed: Q16.3, R30.1, U2.9
unnamed: R3.1, U4.3
unnamed: R18.2, U2.2, U3.4
unnamed: R19.2, U2.13, U5.4
unnamed: R29.2, U2.1, U3.10
unnamed: R31.2, U2.14, U5.10
unnamed: RV1.2, U4.1
unnamed: U1.1, U7.3
unnamed: U1.2, U7.6
unnamed: U1.4, U7.8
unnamed: U1.5, U7.11
unnamed: U1.9, U8.3
unnamed: U1.10, U8.6
unnamed: U1.12, U8.8
unnamed: U1.13, U8.11
unnamed: U3.6, U7.4
unnamed: U3.8, U7.12
unnamed: U5.6, U8.4
unnamed: U5.8, U8.12
PWM: U4.6, U7.1, U7.9, U8.1, U8.9
PWR_GND: C1.1, C2.2, C3.1, C4.1, C5.1, D1.1, D2.1, D4.1, D5.1, D6.1, D7.2, J1.2, J3.1, J4.1, J5.1, J6.1, Q1.2, Q2.2, Q3.2, Q4.2, Q9.2, Q10.2, Q11.2, Q12.2, R1.1, R3.2, R16.2, R17.2, R28.2, R30.2, RV1.3, RV2.3, U1.7, U2.12, U3.2, U3.3, U3.7, U3.11, U3.12, U4.2, U5.2, U5.3, U5.7, U5.11, U5.12, U6.2, U7.7, U8.7
VBAT: D8.1, D9.1, D10.1, D11.1, F1.2, F2.1, J2.1, J2.3, J2.5, J2.7, R1.2, R6.2
VBAT_IN: F1.1, J1.1
VREF: RV2.2, U2.4, U2.6, U2.8, U2.10
inv_INJ1: Q1.3, Q3.1, R10.2, U3.1, U7.2, U7.5
inv_INJ2: Q9.3, Q11.1, R22.2, U3.13, U7.10, U7.13
inv_INJ3: Q2.3, Q4.1, R11.2, U5.1, U8.2, U8.5
inv_INJ4: Q10.3, Q12.1, R24.2, U5.13, U8.10, U8.13

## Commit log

2020-07-13 Initial commit
    First commit after making a separate repository for the peak and hold driver.
    [PeakHoldPWMDriver-B_Cu.gbr, PeakHoldPWMDriver-B_Mask.gbr, PeakHoldPWMDriver-B_Paste.gbr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]
2020-07-13 Routing board V0.2
    Work done on new PCB
    [PeakHoldPWMDriver.kicad_pcb, PeakHoldPWMDriver.sch]
2020-07-14 routed V0.2
    New board fully routed
    [PeakHoldPWMDriver.kicad_pcb, PeakHoldPWMDriver.sch]
2020-07-16 Cleanup of board
    [PeakHoldPWMDriver.csv, PeakHoldPWMDriver.kicad_pcb, PeakHoldPWMDriver.sch]
2020-07-19 further clean-up
    [BOM_PeakHoldPWMDriver_V0.2.csv, PeakHoldPWMDriver.csv, PeakHoldPWMDriver.kicad_pcb]
2020-07-19 renumber all parts
    [BOM_PeakHoldPWMDriver_V0.2.csv, PeakHoldPWMDriver.kicad_pcb, PeakHoldPWMDriver.sch]
2020-07-29 Started on V0.3
    - update on simulation
    - started design V0.3
    - input protection
    - Zener clamping on mosfet gate
    [BOM_PeakHoldPWMDriver_V0.2.csv, PeakHoldPWMDriver.kicad_pcb, PeakHoldPWMDriver.sch]
2020-07-29 cleaup
    cleanup of silkscreen
    [PeakHoldPWMDriver.kicad_pcb, PeakHoldPWMDriver.sch]
2020-07-31 Added jumpers to choose between ECU or transistor input
    [PeakHoldPWMDriver.kicad_pcb, PeakHoldPWMDriver.sch]
2020-07-31 clean-up pcb
    [PeakHoldPWMDriver.kicad_pcb]
2020-08-01 Updates on V0.3
    Updated V0.3
    - Created readme
    - Cleaned up baord.
    - Created gerbers
    [BOM_PeakHoldPWMDriver_V0.2.csv, BOM_PeakHoldPWMDriver_V0.3.csv, PeakHoldPWMDriver.kicad_pcb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]
2020-08-02 Added supplier to BOM list
    [BOM_PeakHoldPWMDriver_V0.3.csv, PeakHoldPWMDriver.kicad_pcb, PeakHoldPWMDriver.sch]
2020-08-04 Update V0.3 PCB
    Updated V0.3 pcb with pulldown resistors when using ECU input. And some Cleanup pcb
    [BOM_PeakHoldPWMDriver_V0.3.csv, BOM_PeakHoldPWMDriver_V0.3.ods, PeakHoldPWMDriver.kicad_pcb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]
2020-08-04 Update zener value
    [PeakHoldPWMDriver.kicad_pcb, PeakHoldPWMDriver.sch]
2020-08-05 update on p-chan mosfets
    Overheating issues hopefully solved by this mod
    [PeakHoldPWMDriver.kicad_pcb, PeakHoldPWMDriver.sch]
2020-08-07 Updates on schematic and pcb because of heat
    [BOM_PeakHoldPWMDriver_V0.3.csv, BOM_PeakHoldPWMDriver_V0.3.ods]
2020-08-07 Simulating 2 pmos fets as high side driver
2020-08-07 Added battery voltage compensation to the simulation
2020-08-07 PCB and schematic updated with battery voltage compensation
    [PeakHoldPWMDriver.kicad_pcb, PeakHoldPWMDriver.sch]
2020-08-07 Some leftover updates
    [PeakHoldPWMDriver.sch]
2020-09-01 updates values on 0.3 added 0.3.1
    Updated resistor values for V0.3
    Added V0.3.1 with new battery voltage compensation
    [PeakHoldPWMDriver-B_Cu.gbr, PeakHoldPWMDriver-B_Mask.gbr, PeakHoldPWMDriver-B_Paste.gbr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]
2020-09-01 Update parts V0.3.1
    [PeakHoldPWMDriver.kicad_pcb, PeakHoldPWMDriver.sch, PeakHoldPWMDriver_V0.3.1.csv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]
2020-09-06 Add pdf schematic
    [PeakHoldPWMDriver.kicad_pcb, PeakHoldPWMDriver_V0.3.1.ods, PeakHoldPWMDriver_V0.3.1_jlcpcb.csv]
2020-09-13 Changed resistor value R5, now correct PWM freqency
    [PeakHoldPWMDriver.kicad_pcb, PeakHoldPWMDriver.sch, PeakHoldPWMDriver_V0.3.1.ods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]
2020-10-07 Add version V0.3.2
    [PeakHoldPWMDriver.kicad_pcb, PeakHoldPWMDriver.sch, PeakHoldPWMDriver_V0.3.1.ods]
2020-11-11 Update schematic for clarity
    [PeakHoldPWMDriver.kicad_pcb, PeakHoldPWMDriver.sch]
2021-02-08 Update schematic with JLCPCB part numbers Added position csv and BOM files in JLCPCB placement list format
2021-02-08 Added position csv and BOM files in JLCPCB placement list format
    [PeakHoldPWMDriver.kicad_pcb, PeakHoldPWMDriver.sch, PeakHoldPWMDriver_V0.3.1.ods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]
